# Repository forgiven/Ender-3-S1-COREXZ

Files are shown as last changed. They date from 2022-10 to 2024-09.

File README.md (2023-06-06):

# Ender 3 S1 COREXZ

## Version 2.1
---

## ***** IMPORTANT NOTE *****
### - This is `NOT` an easy / user friendly build. You have to remove the heated bed to fit the stepper mounts!
### - Also you have to rotate the top 2020 frame aluminium extrusion so the v-slot faces the front.
### - You would have to configure Klipper or Marlin to work using `corexz` kinematics

## ******************
---

After some contemplating, I have decided to create a version 2 of the Ender 3 S1 corexz kinematics. It has a compact footprint, shorter belt path and more rigid design, albeit more sophisticated.

The three main motivations for version 2 were:
- Print quality focused
- Compact design
- Challenge CAD capabilities xd

Not a very high bar was set, but I achieved it and seems to have higher X-axis acceleration than previous versions (now ~13 000 compared to ~8000 before)

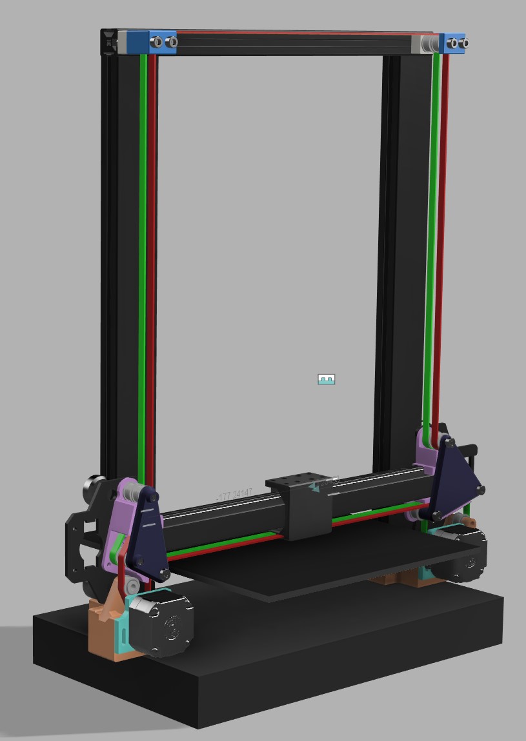
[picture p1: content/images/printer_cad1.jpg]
Cad images

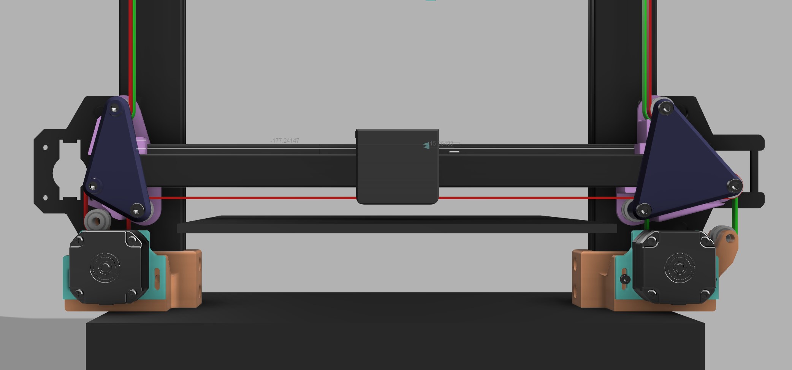
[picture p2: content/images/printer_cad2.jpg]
Cad images

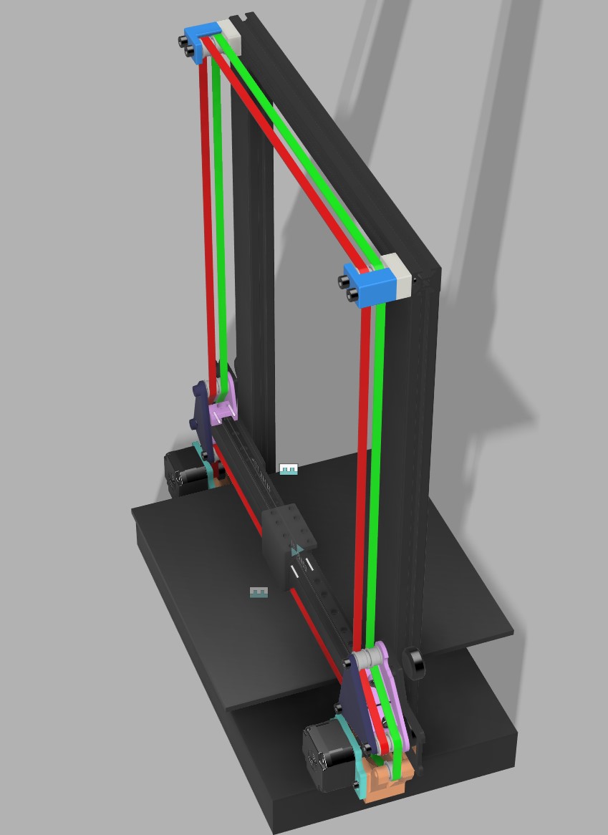
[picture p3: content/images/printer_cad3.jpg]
Cad images

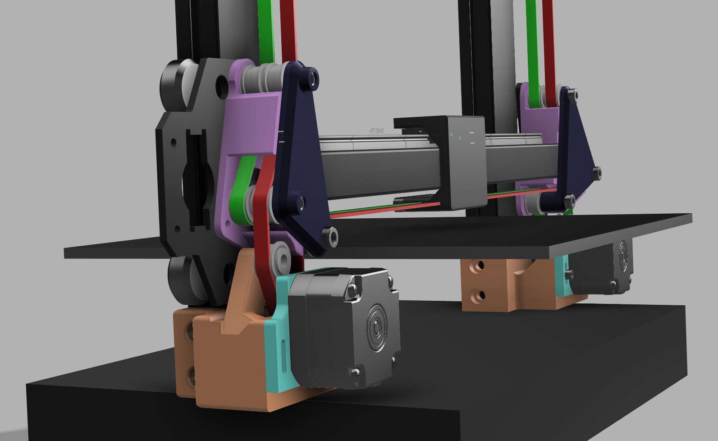
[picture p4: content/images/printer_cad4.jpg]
Cad images

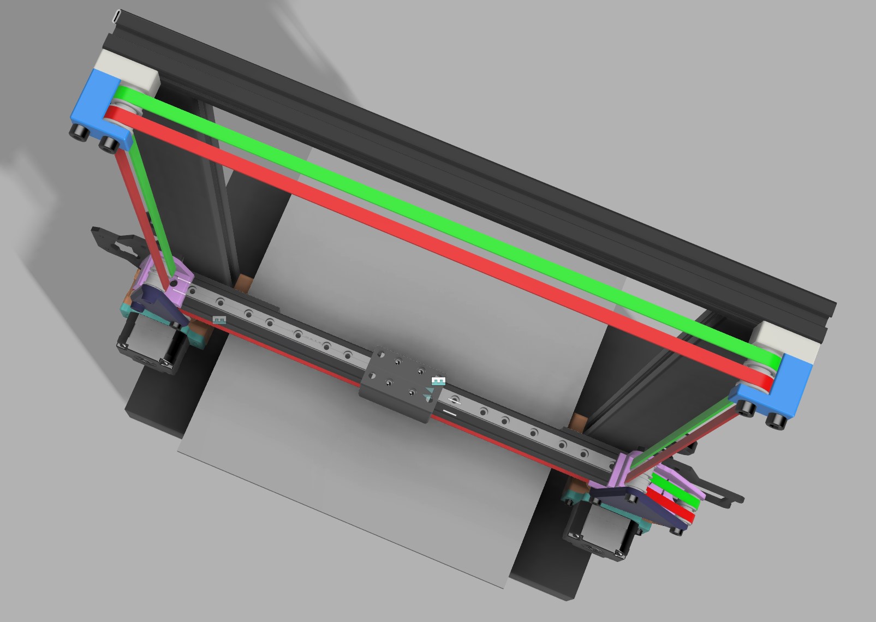
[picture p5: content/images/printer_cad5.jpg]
Cad images


---

## Print orientation / settings

STL's can be found in the `stl` folder or on [Printables](https://www.printables.com/model/492543-ender-3-s1-corexz-v21)

Filament:
- Printed all the parts in eSUN PLA+ (EXCEPT the stepper flanges)
- Stepper motor flanges were printed in PETG (to withstand stepper motor heat)

### Slicer settigns
- 0.4mm nozzle
- 0.2mm first layer height
- 0.24mm layer height for the rest
- 3 walls, 4 top, 3 bottom
- 0.42mm line width (default, internal solid infill, supports)
- 0.45mm line width (first layer, inner wall, outer wall, top surface, sparse infill)
- 20% grid infill for PLA parts, 20% gyroid infill for PETG
- Supports only needed for right gantry cover
    - normal snug supports
    - only on build plate

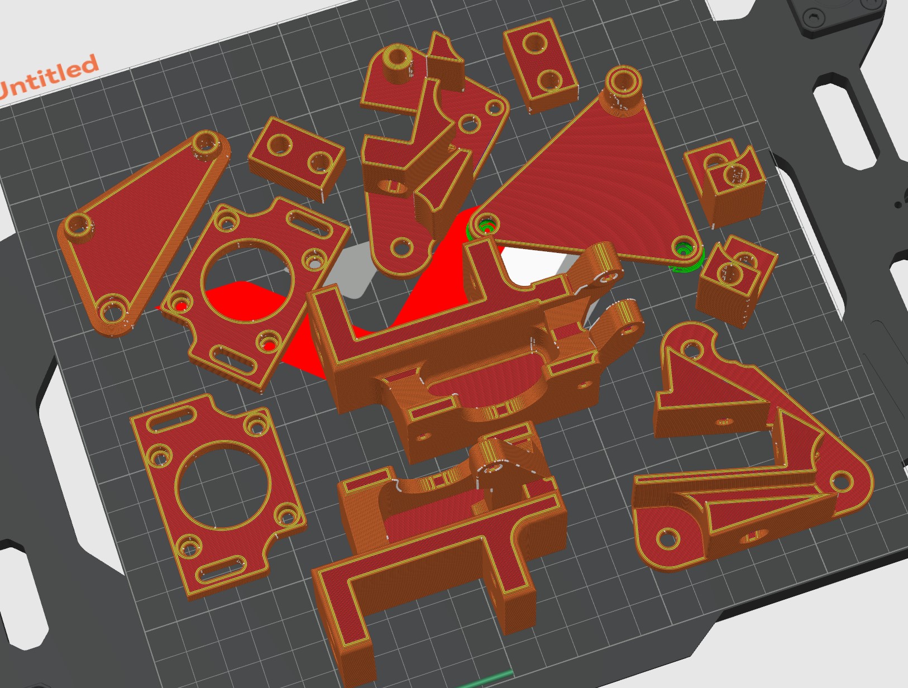
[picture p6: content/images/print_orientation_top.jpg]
Print orientation top


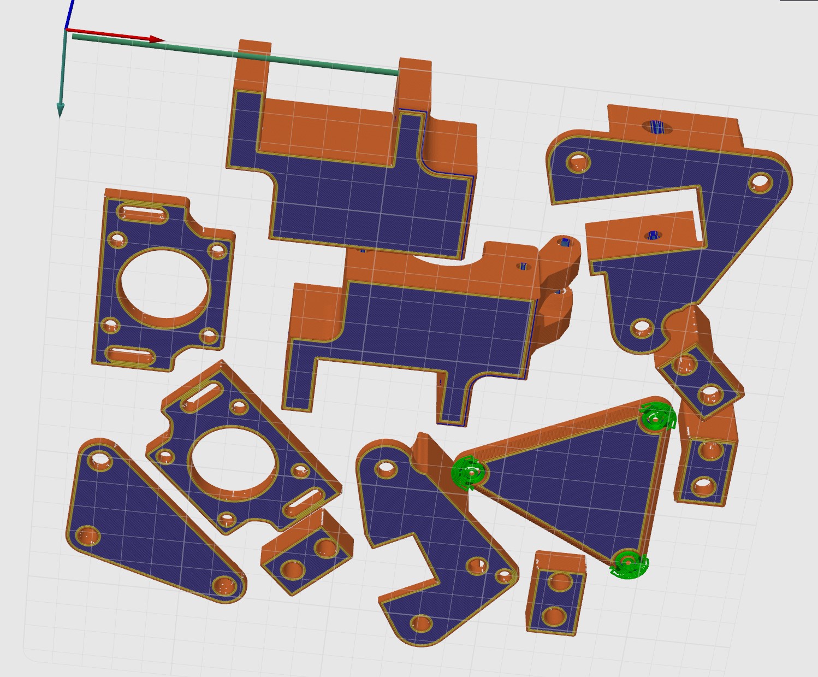
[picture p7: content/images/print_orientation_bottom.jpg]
Print orientation bottom


# Some prints using V2.1 Corexz

See it in action on my [youtube channel](https://www.youtube.com/@f0rgiv3n)

### Cali dragon
- 0.2 layer height
- 4k accelerations (limited by bed slinging Y-axis)
- 200mm/s inner walls
- 120mm/s outer walls
- square corner velocity 5 external, 9 internal

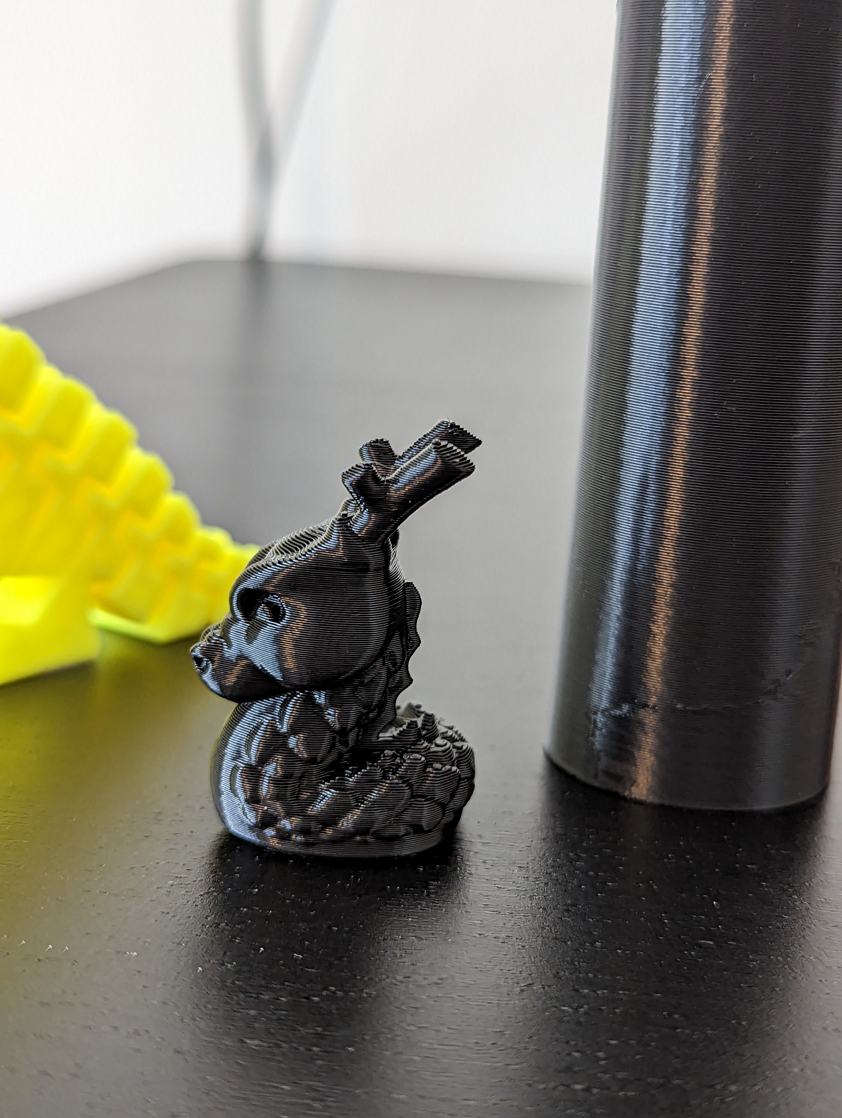
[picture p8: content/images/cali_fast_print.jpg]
Cali dragon


### Z-axis accuracy, target 200mm -> result 200mm

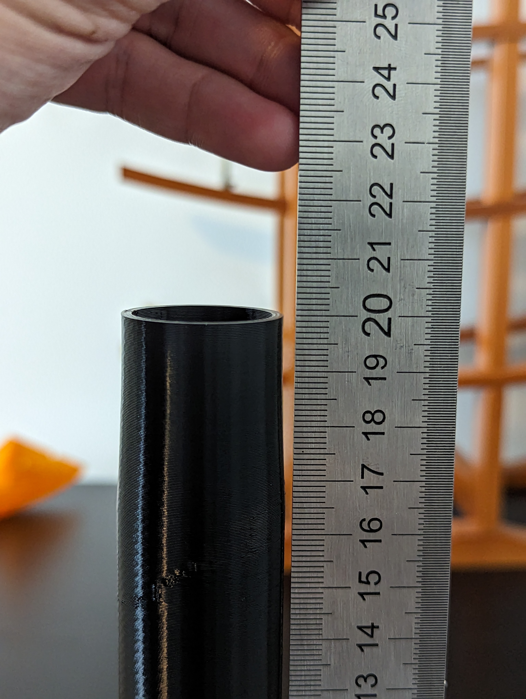
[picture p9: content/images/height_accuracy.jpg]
Z-axis accuracy


### Uniform Z-layers
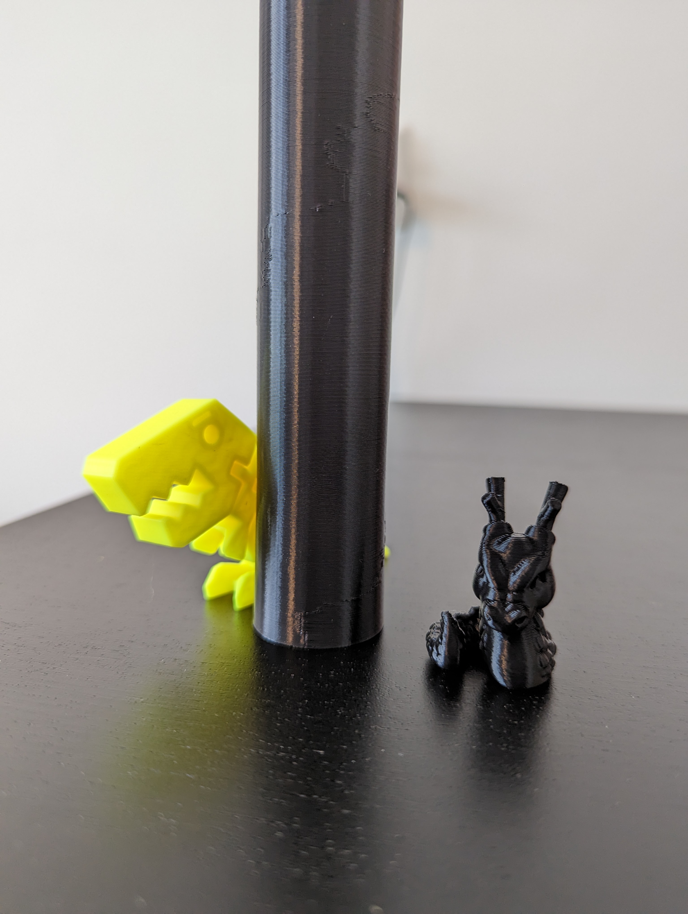
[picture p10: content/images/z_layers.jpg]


---

## Thanks
If you find any of my work useful or fun and want to say thanks in any way, feel free to buy me a beer or a coffee .. it definitely cost me a few of those while working on this project :P

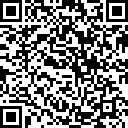
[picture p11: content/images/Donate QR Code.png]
Buy me a beer or coffee (https://www.paypal.com/donate/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)


https://www.paypal.com/donate/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

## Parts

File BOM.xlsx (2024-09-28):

Item | Notes | Link
GT2 Belt – 6mm wide | 4m | https://www.amazon.nl/gp/product/B07QNWJ1XC/ref=ppx_yo_dt_b_asin_title_o01_s00?ie=UTF8&psc=1
F695 2RS Bearing 5*13*4 | x32 | https://www.aliexpress.com/item/33001186278.html
Stainless steel Flat Washer 5x10 – 1mm thick | x32 | https://www.aliexpress.com/item/32917948919.html
20 Series T Nuts M5 T Slot Nuts | x8 | https://www.amazon.nl/-/en/gp/product/B086JYFXPW/ref=ppx_yo_dt_b_search_asin_title?ie=UTF8&psc=1
M3 M5 Hex Socket Bolts / Nuts (5mm – 30mm) | x20 | https://www.amazon.nl/-/en/gp/product/B08M5TSLCN/ref=ppx_yo_dt_b_search_asin_title?ie=UTF8&psc=1
Brass Threaded Inserts |  | https://www.amazon.nl/-/en/gp/product/B09B7F2XM3/ref=ppx_yo_dt_b_search_asin_title?ie=UTF8&psc=1
NEMA17 stepper motors | x2 | https://www.amazon.nl/-/en/gp/product/B07SQNYZDY/ref=ppx_yo_dt_b_search_asin_title?ie=UTF8&th=1
GT2 Timing Belt Pulley 20 tooth, 6mm width, 5mm bore | x2 | https://www.aliexpress.com/item/10000046456013.html?curPageLogUid=09OYRIFzKRYK

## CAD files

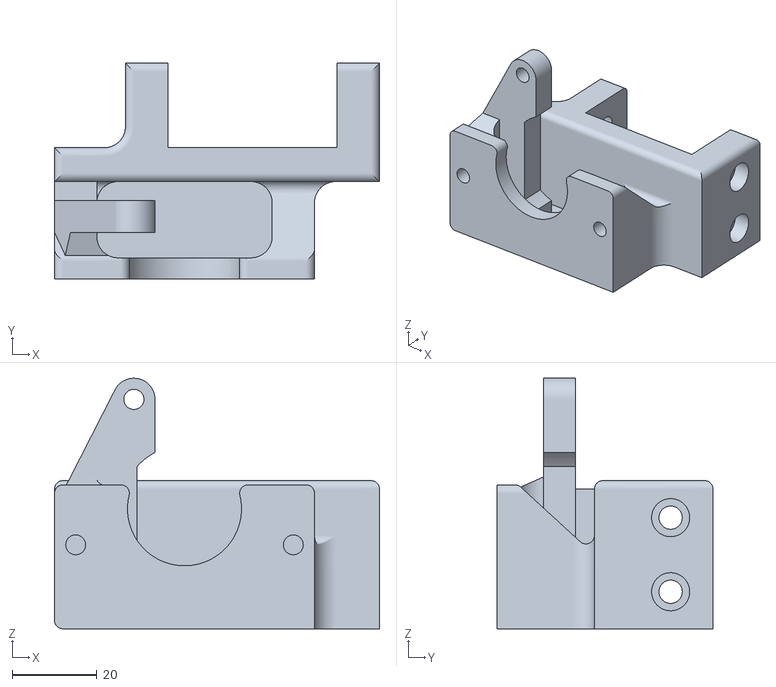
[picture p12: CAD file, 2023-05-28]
stl/Left motor mount.stl
76.8 x 51.0 x 59.2

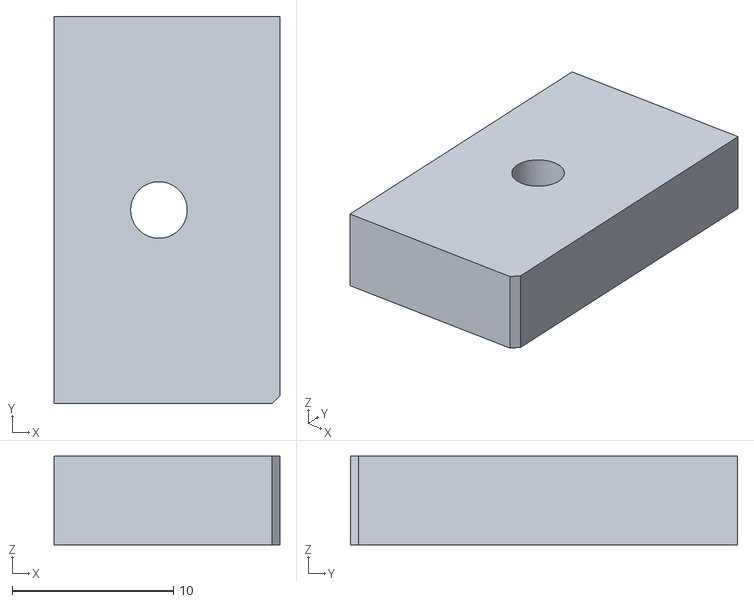
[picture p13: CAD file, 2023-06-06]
stl/mgn9h_x_mount/Right clamp.stl
14.0 x 24.0 x 5.50

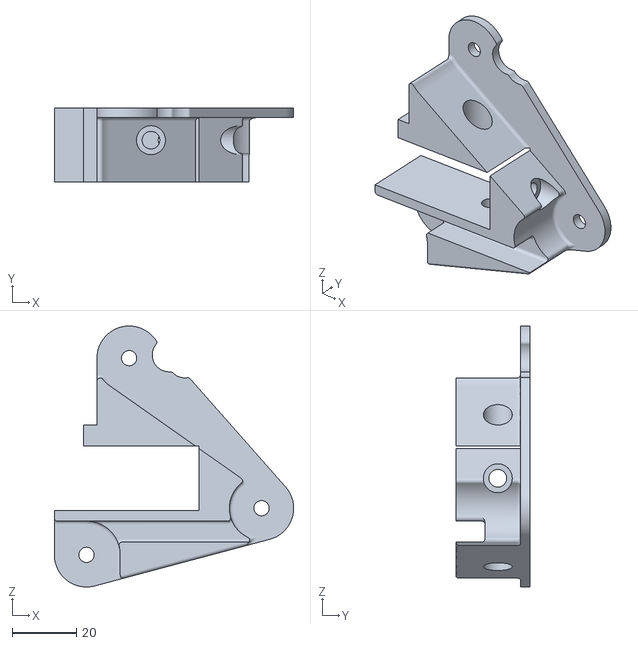
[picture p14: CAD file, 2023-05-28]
stl/Right gantry mount.stl
74.4 x 23.0 x 81.2

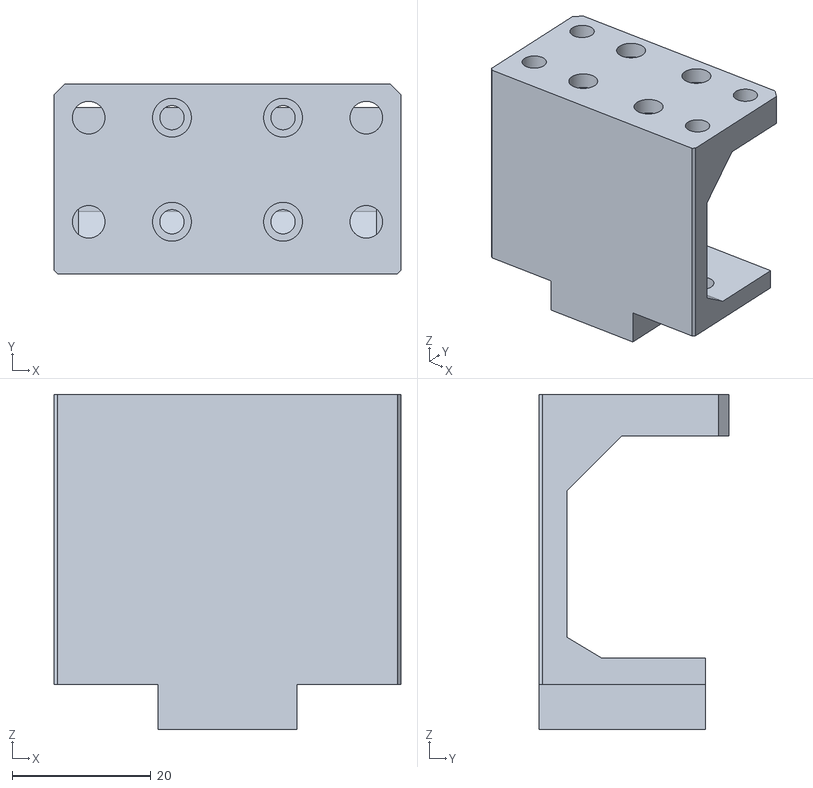
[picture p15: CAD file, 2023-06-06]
stl/mgn9h_x_mount/Mount.stl
50.0 x 27.3 x 48.3

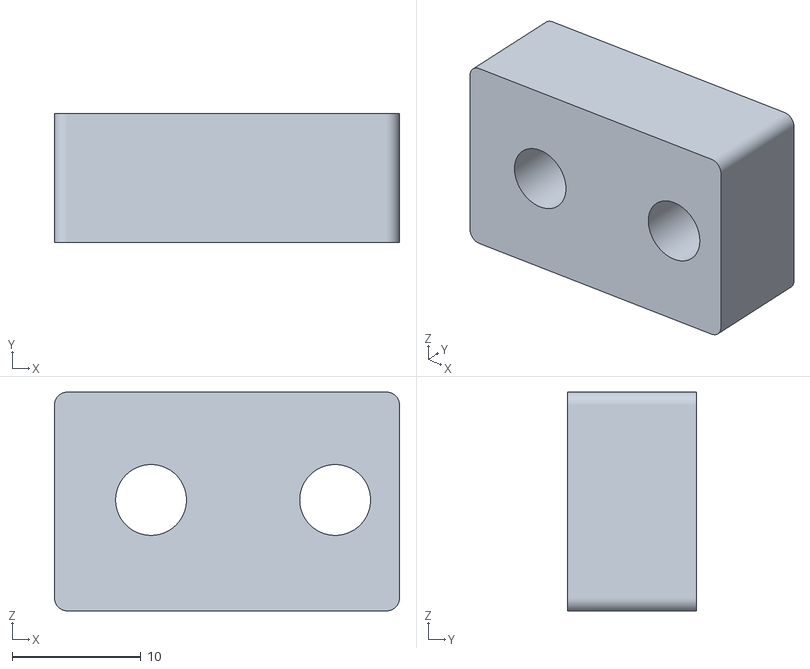
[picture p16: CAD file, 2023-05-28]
stl/Top right pulley back.stl
26.8 x 10.00 x 17.0

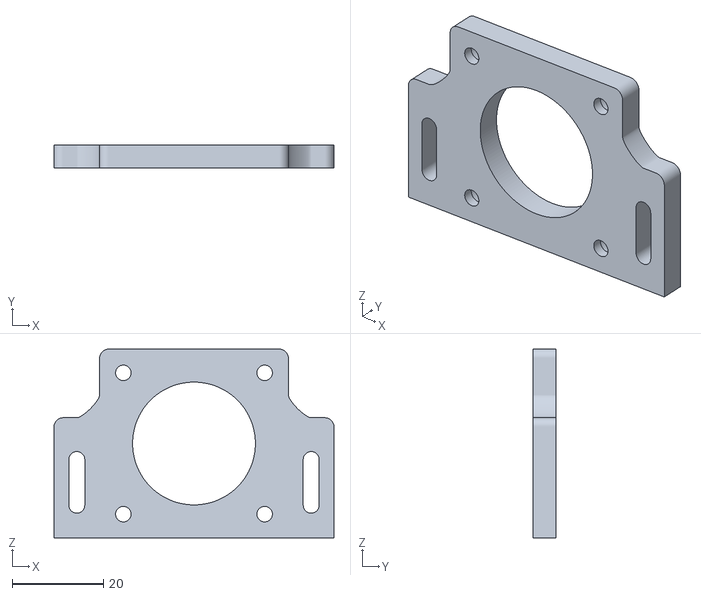
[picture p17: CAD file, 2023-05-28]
stl/Left motor flange.stl
61.4 x 5.00 x 41.4

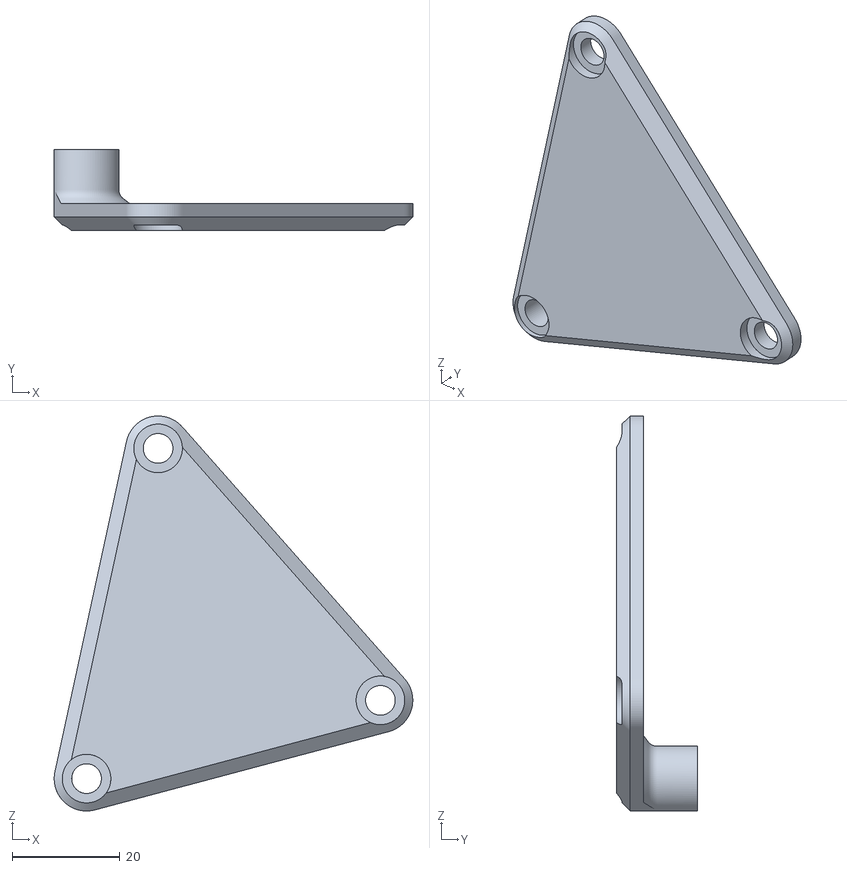
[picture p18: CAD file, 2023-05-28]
stl/Right gantry cover.stl
66.4 x 15.0 x 73.2

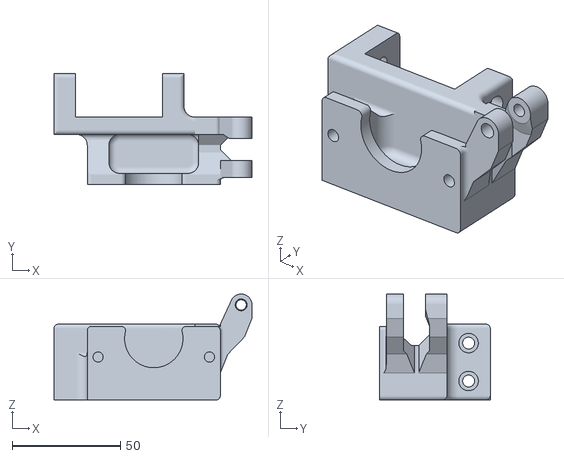
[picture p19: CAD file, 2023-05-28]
stl/Right motor mount.stl
91.4 x 51.0 x 48.9

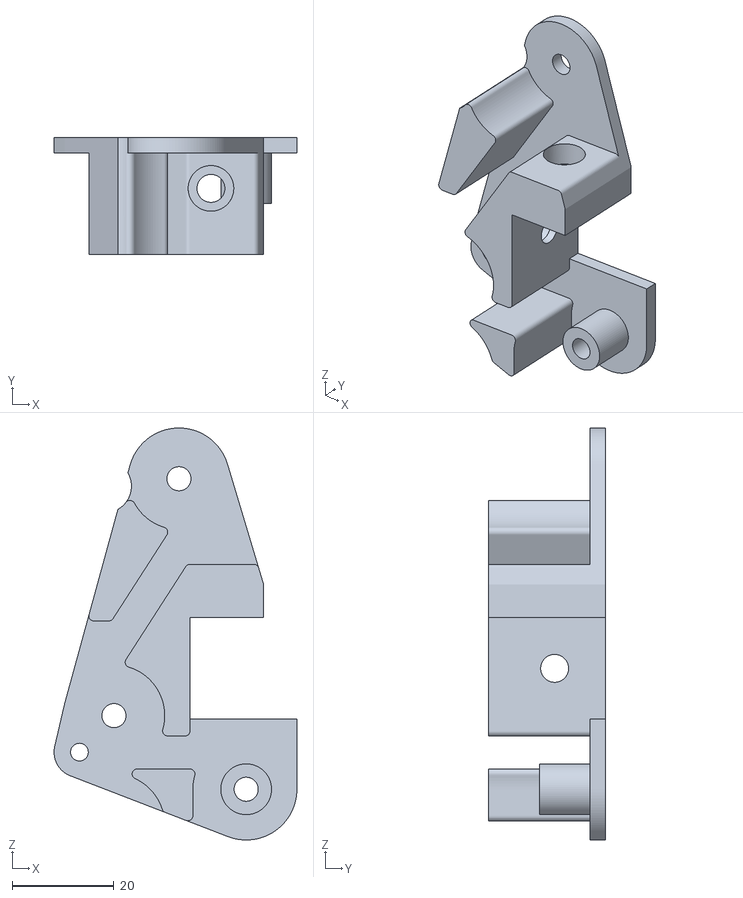
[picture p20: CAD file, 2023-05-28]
stl/Left gantry mount.stl
47.9 x 23.0 x 81.2

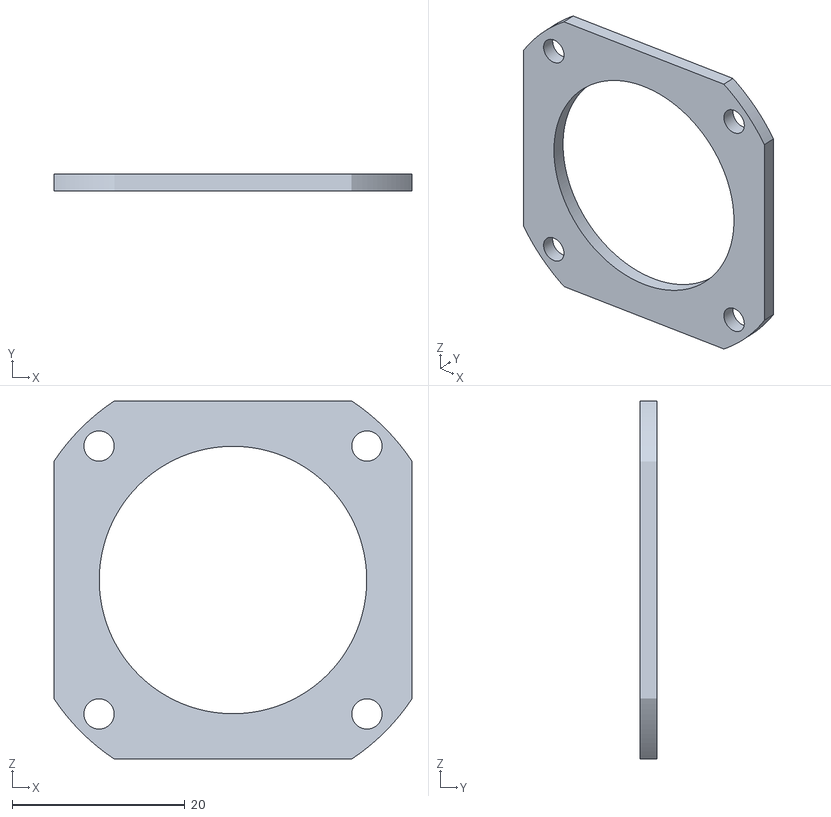
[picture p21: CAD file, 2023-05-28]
stl/Stepper TPU Spacer (optional).stl
41.4 x 2.00 x 41.4

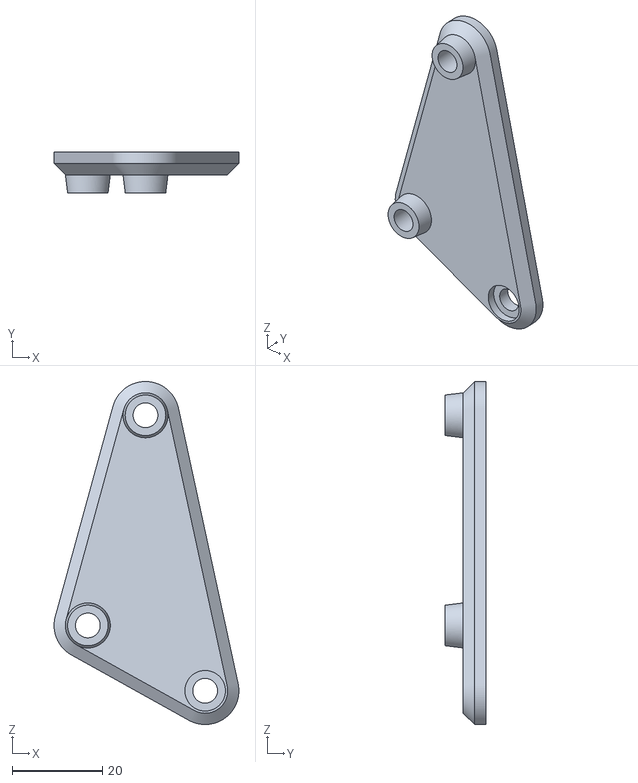
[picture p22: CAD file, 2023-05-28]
stl/Left gantry cover.stl
41.1 x 9.00 x 76.2

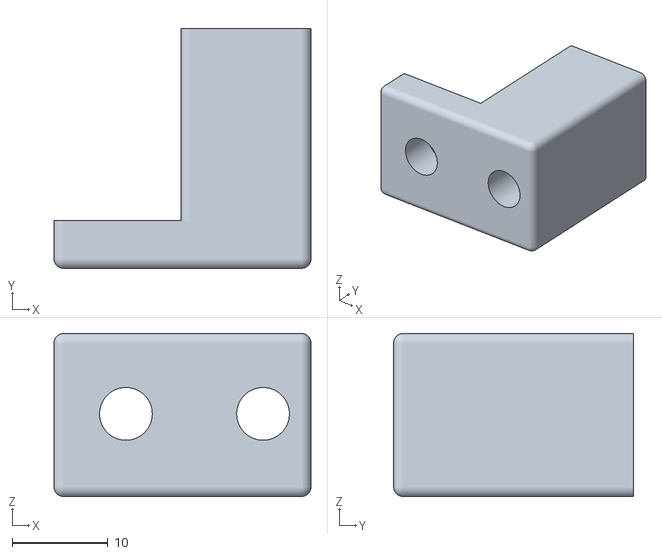
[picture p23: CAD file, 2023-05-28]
stl/Top right pulley front.stl
26.8 x 25.0 x 17.0

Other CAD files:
stl/mgn9h_x_mount/Left clamp.stl
stl/Right motor flange.stl
stl/Top left pulley back.stl
stl/Top left pulley front.stl

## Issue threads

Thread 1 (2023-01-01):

Motor Mount issues and request for Keyback

ArtemisStiles, 2023-01-01:
Excellent mod, I would like to start with. My S1 has never been more consistent and it's running faster than even. Unfortunately, I've noticed a fairly major flaw with how it's designed currently.

The Motor Mounts deform over the length of a print when made from PETG, especially on the Z axis (right) side.

Now there are a couple of solutions that come to mind, those being use ABS and/or reduce the stepper voltage via the potentiometer on the main board, but my assumption is that the goal is accessibility with this mod, so I thought one should be made aware.

Another flaw I have noticed (and I know you probably have too) is the lack of a Z axis retention system in the case of a power loss or when the steppers turn off at idle. The Switchwire uses a Keyback retractable key ring to solve this issue, but that can't work with the current design and would likely involve redesigning a mount or two. Still, this is a fairly important feature in preventing wear and damage to the Toolhead and bed, so if you are still looking to improve the design I highly request this become an added feature.

forgiven, 2023-01-04:
Hey thanks for the feedback! To answer your suggestions:
**"The Motor Mounts deform over the length of a print when made from PETG, especially on the Z axis (right) side."**
  - I have not had any issues with motor mounts deforming with PETG, be sure to use 4 external perimeters and around 50% grid infill. Maybe your stepper motors are running too hot? Mine will get quite warm over long periods of time, but no warping with the PETG stepper motor mounts.

**"Another flaw I have noticed (and I know you probably have too) is the lack of a Z axis retention system"**
 - This is correct, I have attached one on my printer, it does not work very well, but it does help, I will look at making a more suitable mount for it.

My time for this project is limited unfortunately, so updates could take a while.

ArtemisStiles, 2023-01-09:
Following up, thank you for replying!

**"Maybe your stepper motors are running too hot?"**

- It turns out that due to the dual Z system that Creality used, VREF for Z was set to 1.5v (yikes!). I tuned it down to 1.2v in line with the X and Y VREFs and we shall see if that helps. I already replaced the mounts with ABS, so I highly doubt those will melt, but at the very least the Z stepper should remain cooler.

**"...I will look at making a more suitable mount for it."**

- Awesome, that will make a better experience overall with this system. One thought would be to include it as part of the right motor mount (more room), run it up to a pulley on the top mount (through the old Z screw hole perhaps?), then run it down to a mount on the back of the V roller bracket. With one of the heavier Keybacks (like the 14oz, though I think I saw a 30oz one too?) it should perform rather well, as it would be similar to the Voron SW Keyback system.

**"My time for this project is limited unfortunately, so updates could take a while."**

- No worries! I am just trying to contribute how I can. I love what you have done with this so far, and despite the growing pains, I patiently look forward to what else you can think of!

Closed 2023-04-13.

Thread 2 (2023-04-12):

X carriage step files and number of teeth on the XZ steppers

BGurUpei, 2023-04-12:
the title says it, I was wondering how you made 2 gt2 belts fit per side on the x carriage also you included the klipper config, but in the BOM the gt2 adapters for the steppers are not listed, so I'm wondering what you used, since on the gantry the tolerances are fairly tight and I want to make sure I have proper tolerances for the belt

forgiven, 2023-04-13:
Hello, I have updated to BOM to include the motors, you can use any nema 17 motors that come with most ender 3 printers. Though you need to align the pulleys with the gantry belt pulleys. You need to know the spec of your stepper motors to configure them accordingly.

The gantry pulleys are comprised of the F695 2RS Bearings (5*13*4) and Stainless steel Flat Washer (5x10x1) and kept in place with an M5 bolt. I have updated the onshape assembly to give some idea. Hope this helps.

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

Closed 2023-04-20.

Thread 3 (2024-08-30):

Modification if being used in V2 instead

dhupee, 2024-08-30:
Hey, great mod you got there

so I'm planning to klipperize and corexz my Ender 3 V2, found this mod and I like it, but I have few questions

1. regarding the difference in S1 and V2 what do you think parts that might need be created differently or at least modified
2. Why PLA+ and not ABS like Voron has, isnt PLA+ gonna soft and creeping for this sort of usage

forgiven, 2024-08-30:
Hi there

Thanks!

To answer your questions:
    1. This mod is quite particular to the Ender 3 S1. I never owned an Ender 3 V2 so I cannot say what work would be required.
    2. ABS can also work fine, I did not have a printer that could print ABS, but should be more suitable.

I've made the `.step` file available if anyone would like to adapt it to their needs.

dhupee, 2024-08-30:
That's more than enough, I appreciate that you answer

Typical Ender 3 like V2 that I own should be able to print ABS, but with draft or mouse ears to maximize the results, but I need to research more

But really the fact that you share the step file is more than enough

Thanks a lot, starred

Closed 2024-08-30.

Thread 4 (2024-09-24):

No mention of the linear rail in BOM

jamincollins, 2024-09-24:
SSIA

forgiven, 2024-09-25:
Hi.

This is not a requirement for conversion.

Closed 2024-09-25.

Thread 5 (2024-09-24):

No project license listed

jamincollins, 2024-09-24:
The printables link for the parts shows:
https://creativecommons.org/licenses/by-nc-sa/4.0/

I'm asking for license clarifications as I would like to potentially add some improvements to this project, but need to clarify the license terms as some of the additions might be derivatives of GPLv3 based works.  And GPLv3 and CC BY-NC-SA 4.0 are not compatible with one another:

> Currently, no non-CC licenses have been designated as compatible with BY-NC-SA 4.0. Other licenses may be added to this list at any time according to the established [process and criteria](http://wiki.creativecommons.org/ShareAlike_compatibility_process_and_criteria). Once a license has been added to this list, it will not be removed.

However, if the **NC** part of the license terms is dropped then it is compatible with the GPLv3:

> GPLv3: The [GNU General Public License version 3 ](https://www.gnu.org/copyleft/gpl.html)was declared a “BY-SA–Compatible License” for version 4.0 on 8 October 2015. Note that compatibility with the GPLv3 is one-way only, which means you may license your contributions to adaptations of BY-SA 4.0 materials under GPLv3, but you may not license your contributions to adaptations of GPLv3 projects under BY-SA 4.0. Other [special considerations](https://wiki.creativecommons.org/wiki/ShareAlike_compatibility:_GPLv3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) apply. See the full [analysis](https://wiki.creativecommons.org/wiki/ShareAlike_compatibility:_GPLv3) and [comparison](https://wiki.creativecommons.org/wiki/ShareAlike_compatibility_analysis:_GPL) for more information.

Reference:
https://creativecommons.org/share-your-work/licensing-considerations/compatible-licenses

forgiven, 2024-09-25:
Hi.

The license is the one defined on Printables.

Closed 2024-09-25.

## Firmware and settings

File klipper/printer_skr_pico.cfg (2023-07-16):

# Enable object exclusion
[exclude_object]

# Enable arcs support
[gcode_arcs]
resolution: 0.1

[stepper_x]
step_pin: gpio11
dir_pin: !gpio10
enable_pin: !gpio12
microsteps: 16
rotation_distance: 40
full_steps_per_rotation: 200
endstop_pin: tmc2209_stepper_x:virtual_endstop
homing_retract_dist: 0
position_min: -2
position_endstop: -2
position_max: 225
homing_speed: 50

[tmc2209 stepper_x]
uart_pin: gpio9
tx_pin: gpio8
uart_address: 0
run_current: 0.7
stealthchop_threshold: 0
interpolate: True
diag_pin: ^gpio4
driver_SGTHRS: 110

[stepper_y]
step_pin: gpio6
dir_pin: !gpio5
enable_pin: !gpio7
microsteps: 16
rotation_distance: 40
full_steps_per_rotation: 200
endstop_pin: tmc2209_stepper_y:virtual_endstop
homing_retract_dist: 0
position_min: -15
position_endstop: -15
position_max: 230
homing_speed: 50

[tmc2209 stepper_y]
uart_pin: gpio9
tx_pin: gpio8
uart_address: 2
run_current: 0.85
stealthchop_threshold: 0
interpolate: True
diag_pin: ^gpio3
driver_SGTHRS: 110

[stepper_z]
step_pin: gpio19
dir_pin: !gpio28
enable_pin: !gpio2
microsteps: 16
rotation_distance: 40
full_steps_per_rotation: 200
endstop_pin: probe:z_virtual_endstop
position_min: -2.0
position_max: 250

[tmc2209 stepper_z]
uart_pin: gpio9
tx_pin: gpio8
uart_address: 1
run_current: 0.7
stealthchop_threshold: 0
interpolate: True
diag_pin: ^gpio25

##
## HX Extruder 
##
[extruder]
step_pin: gpio14
dir_pin: !gpio13
enable_pin: !gpio15
microsteps: 16
rotation_distance: 4.435
full_steps_per_rotation: 200
nozzle_diameter: 0.4
filament_diameter: 1.75
heater_pin: gpio23
sensor_type: EPCOS 100K B57560G104F
sensor_pin: gpio27
control: pid
pid_Kp: 22.2
pid_Ki: 1.08
pid_Kd: 114
min_temp: 0
max_temp: 300
max_extrude_only_distance: 300
max_extrude_cross_section: 5

[tmc2209 extruder]
uart_pin: gpio9
tx_pin: gpio8
uart_address: 3
run_current: 0.60
stealthchop_threshold: 0
interpolate: True

[filament_switch_sensor runout_sensor]
switch_pin: ^gpio16
pause_on_runout: True

[heater_bed]
heater_pin: gpio21
sensor_type: EPCOS 100K B57560G104F
sensor_pin: gpio26
control: pid
pid_Kp: 54.027
pid_Ki: 0.770
pid_Kd: 948.182
min_temp: 0
max_temp: 100

[fan]
pin: gpio17

[heater_fan hotend_fan]
pin: gpio18
heater: extruder
heater_temp: 50.0
fan_speed: 0.85

[fan_generic SKR_Fan]
pin: gpio20
max_power: 1.0

[mcu]
#serial: /dev/serial/by-path/<mcu>
restart_method: command

[temperature_sensor SKR_Pico]
sensor_type: temperature_mcu
min_temp: 0
max_temp: 100

[temperature_sensor RPI4]
sensor_type: temperature_host
min_temp: 0
max_temp: 100

[printer]
kinematics: corexz
max_velocity: 500
max_accel: 4000
max_accel_to_decel: 2000
max_z_velocity: 200
max_z_accel: 4000
square_corner_velocity: 5

[probe]
pin: !gpio22
#z_offset: 0
x_offset: -48
y_offset: 8
speed: 10
lift_speed: 25
sample_retract_dist: 3.0
samples: 1


[bed_mesh]
speed: 200
mesh_min: 22, 13
mesh_max: 177, 203
algorithm: bicubic
probe_count: 5,5
horizontal_move_z: 3.0

#[neopixel board_rgb]
#pin: gpio24
#chain_count: 1
#color_order: GRB
#initial_RED: 0.3
#initial_GREEN: 0.3
#initial_BLUE: 0.3

#*# <---------------------- SAVE_CONFIG ---------------------->
#*# DO NOT EDIT THIS BLOCK OR BELOW. The contents are auto-generated.
#*#
#*# [input_shaper]
#*# shaper_type_x = 2hump_ei
#*# shaper_freq_x = 86.4
#*# shaper_type_y = mzv
#*# shaper_freq_y = 37.0
#*#
#*# [probe]
#*# z_offset = 1.535

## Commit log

2022-09-17 initial stls
    [left gantry mount.stl, left stepper mount.stl, left top mount cap.stl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]
2022-09-17 add readme and klipper configs
    [mainsail.cfg, printer.cfg]
2022-09-17 add youtube link to second print
2022-09-21 updated gantry mounts, update readme
    [left gantry mount base.stl, left gantry mount cover.stl, left gantry mount.stl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]
2022-09-21 add klipper config note
2022-10-03 updated to version 1.0, fully functional corexz
    [left gantry mount base.stl, left gantry mount cover.stl, left stepper mount.stl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]
2022-10-03 update onshape url to assembly
2022-12-09 added motor mounts that allow x-axis to move down lower added BOM
    [BOM.xlsx, Left motor mount (lower x-axis).stl, Right motor mount (lower x-axis).stl]
2023-04-13 update bom to include motors + gt2 pulley
    [BOM.xlsx]
2023-04-18 add mgn9h + stealthburner mount
    [MHN9H Extruder Mount Belt Cap.stl, MHN9H Extruder Mount.stl, Stealthburner E3S1 Mount.stl]
2023-04-19 add step files for extruder / stealthburner mount
    [MHN9H Extruder Mount.step, Stealthburner E3S1 Mount.step]
2023-05-28 Ender 3 S1 Corexz v2.1
    [BOM.xlsx, Left gantry cover.stl, Left gantry mount.stl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]
2023-05-28 add printables link
2023-06-06 include x-axis mount
    [Left clamp.stl, Mount.stl, Right clamp.stl]
2023-06-10 minor update to bom.xlsx
    [BOM.xlsx]
2023-07-16 add klipper config
    [printer_skr_pico.cfg]
2024-09-28 update number of bearings required
    [BOM.xlsx]
